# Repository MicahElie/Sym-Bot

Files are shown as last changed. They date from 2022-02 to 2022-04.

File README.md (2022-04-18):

# The Sym-Bot Project: A Robotic Arm by Hand Control 
## Sherbrooke University, Robotics Engineering S4 Project, 66th promotion, Winter 2022


<div align="center">
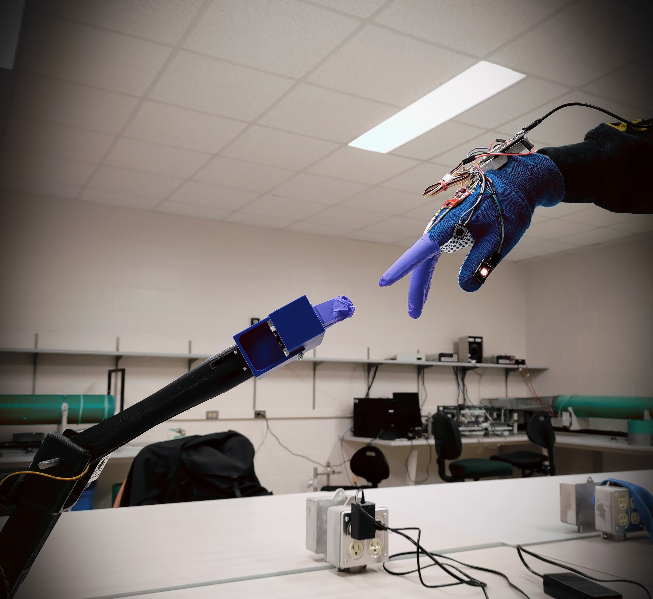
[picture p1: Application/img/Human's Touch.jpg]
Sym-Bot Human's Touch
    
</div>

## Table of Content
- [The Sym-Bot Project: A Robotic Arm by Hand Control](#the-sym-bot-project-a-robotic-arm-by-hand-control)
  - [Sherbrooke University, Robotics Engineering S4 Project, 66th promotion, Winter 2022](#sherbrooke-university-robotics-engineering-s4-project-66th-promotion-winter-2022)
  - [Table of Content](#table-of-content)
  - [Authors](#authors)
  - [Project context](#project-context)
  - [Abilities](#abilities)
  - [Important note](#important-note)
  - [Getting started](#getting-started)
    - [Mechanical recommandations](#mechanical-recommandations)
    - [Electrical recommandations](#electrical-recommandations)
    - [Software recommandations](#software-recommandations)
  - [Special Thanks](#special-thanks)

## Authors
- Andrei Ioan Gabor - [TerrySpooker](https://github.com/TerrySpooker)
- Julien Thériault - [JuThe72](https://github.com/JuThe72)
- Yan-Éric Jérôme - [Arasmith](https://github.com/Arasmith)
- Frank Ciric Taicas - [Chromlox](https://github.com/Chromlox)
- Frédérick Boisvert - [boif1403](https://github.com/boif1403)
- Micah-Élie Labrecque - [MicahElie](https://github.com/MicahElie)

## Project context
This project came up from the desire to help people with disabilities to take or move objects out of reach. 
More precisely, some of these people don't have enough strength in their arms to strech them out. Fortunately, most of the times, they can at least move their hands and fingers.
That's the core of the Sym-Bot Project : Using a glove with sensors to control a robotic arm in the most intuitive way possible, by working in **symbiosis** with the user.

## Abilities
Our robotic arm is a simple 3 degrees of freedom robot. The goal is to accomplish simple tasks only by using the "Glove controller". Here are four things that Sym-Bot can do:
1. Push/Pull an object on the table, placed in front of our robot
2. Turn switch On/Off, the switch being on the table
3. Take a cellphone (200g max.) and keep it in the air
4. Using AI to predict moves based on hand signs that we created

## Important note
Make sure to read all the documentation linked if you want to recreate your own Sym-Bot. 
We'll do anything we can so that the documentation is as clear as possible. First step, read the [Getting started](#getting-started) just below.

## Getting started
The first step to follow for building your own Sym-Bot application is to follow the READMEs step-by-step guide in each sections.
Our project is divided in three main sections: 
* The first one is [Application (Main Software)](Application/), that's **where all the communication and data interpretation between the Glove and the Robotic Arm is done**. In that section, you will mainly find the Python code that will go on the Raspberry Pi 4B (or any other computer of your choice) that will be linked to the OpenCR of the Robotic arm and the Bluetooth of the Glove. That's also where the [AI section](Application/AI/) is.
* The second section is [Robotic Arm](/Robotic%20Arm/), that's where **you'll find the C++ code for the motors control, all the 3D parts with the assembly models (SolidWorks) and the electrical schematic.**
* Finally, the last, but not least, part, is the [Glove User Interface](/Glove%20UI/), in this section **you'll find the C++ code used with PlatformIO on the ESP32 and the list of electrical sensors and components that are attached on the glove with the electrical schematic**.

### Mechanical recommandations
* Most of the parts of our robot arm should be 3D-printed.
* We used different kind of bolts, shafts, inserts and couplers
* We created our own bearing with metalic marbles, but you can easily modify this section
* The list of components to buy, 3D parts and the assembly of the robotic arm is in the [Material & Assembly section](/Robotic%20Arm/Material%20%26%20Assembly/)

### Electrical recommandations
* Most of the electrical part is on the implementation of sensors on the glove
* We personally sew the electrical components on the glove.
* Make sure to use long enough wires for the connection between the motors and the OpenCR
* For more information about the electrical design, look at the [Robotic Arm Electrical schematic](/Robotic%20Arm/Material%20%26%20Assembly/ElectricalSchematic_RoboticArm.png) and the [Glove Electrical schematic](/Glove%20UI/img/Electrical%20Schematic%20Glove.png)

### Software recommandations
* We mostly used Python and C/C++ with Visual Studio Code as code editor and IDE with extensions.

## Special Thanks
To [Handling GRO](https://github.com/chameau5050/Handling-Gro#handling-gro) for their robotic arm that inspired us to make our own.

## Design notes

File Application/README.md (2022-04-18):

# Sym-Bot : Application (Main Software)

## Table of Content
- [Sym-Bot : Application (Main Software)](#sym-bot--application-main-software)
  - [Table of Content](#table-of-content)
  - [Getting started](#getting-started)
  - [Communication](#communication)
    - [BluetoothComm](#bluetoothcomm)
    - [SerialComm](#serialcomm)
    - [Translate](#translate)
  - [AI](#ai)
  - [Interface](#interface)
  - [Test](#test)
    - [test translate class](#test-translate-class)

## Getting started
First, here's the hardware schematic that you have to keep in mind for every aspect of the project:
<div align="center">
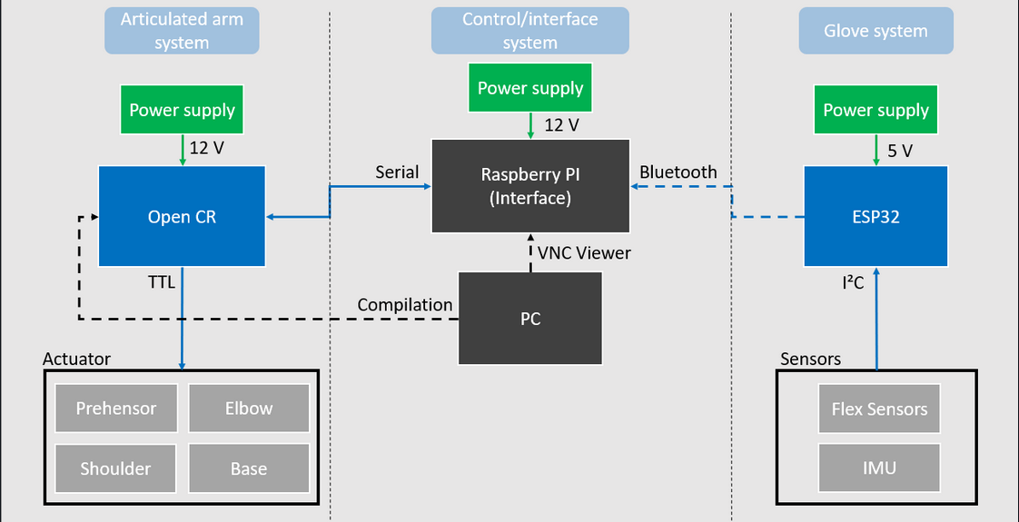
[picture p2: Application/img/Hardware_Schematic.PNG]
Hardware Schematic
    
</div>

***Setup environment***
- Software : [Visual Studio Code](https://code.visualstudio.com/) (Stable Build) and add extension Python, publisher Microsoft
- Using Python version (3.7 and newer)
- Installing packages from the Python with [command line](https://packaging.python.org/en/latest/tutorials/installing-packages/#installing-from-pypi) :
  - numpy (1.22.2)
  - pyserial (3.5)
  - pybluez (0.23)

Single board computer
* Brand : [RaspBerry Pi](https://www.raspberrypi.com/products/raspberry-pi-4-model-b/)
* Model : Raspberry PI 4 B
* Quantity : 1

## Communication
As you know, the Sym-Bot uses an ESP32, a Raspberry Pi 4 and an OpenCR Arduino microcontroller. All the code found in this section allows the communication between thoses devices to be functional. 
### BluetoothComm
Bluetooth Communication is used between Glove UI (ESP32) and Control System (PI4)

Steps to setup Bluetooth device (Must do before you launch main application) :
1. Turn on Bluetooth on Raspberry PI
2. Supply the device Bluetooth
3. Connect ESP32's device on Raspberry PI
4. Collect the informations device
* If you don't know the MAC & uuid device :
Using [rfcomm-client.py's example](https://github.com/pybluez/pybluez/blob/master/examples/simple/rfcomm-client.py) to find MAC & uuid device
5. Write "BT" to select bluetooth communication in main.py
```
10  # Select Communication's type between "USB" (Alternative proto-board UI) or "BT" (Glove)
11  TypeComm = "BT" 
```
6. Change the MAC & uuid device for yours
```
18      ''' Commmunication Bluetooth '''
19      MAC_ = '58:BF:25:37:A6:9A'                        # your MAC BT device
20      uuid_ = "00001101-0000-1000-8000-00805f9b34fb"    # your uuid BT device
```

### SerialComm
Serial communication is used between Control System (PI4) and Robotic Arm (OpenCr)

Steps to setup Serial device (Must do before you launch main application) :
1. Find the Serial Port of OpenCr Board (You can find this information with Arduino IDE -> Tools -> Ports)
2. Change port number on this line:
```
15  messageIO.addDevice(SerialComm("/dev/ttyACM0", 57600))  # Robotic Arm (OpenCr Board)
```
* On Windows OS, the Port Number starts with COM#
* On Linux OS, the Port Number starts with /dev/ttyACM# or /dev/USB#

### Translate
When the Bluetooth communication is established, it should receive messages in this form:
<div align="center">
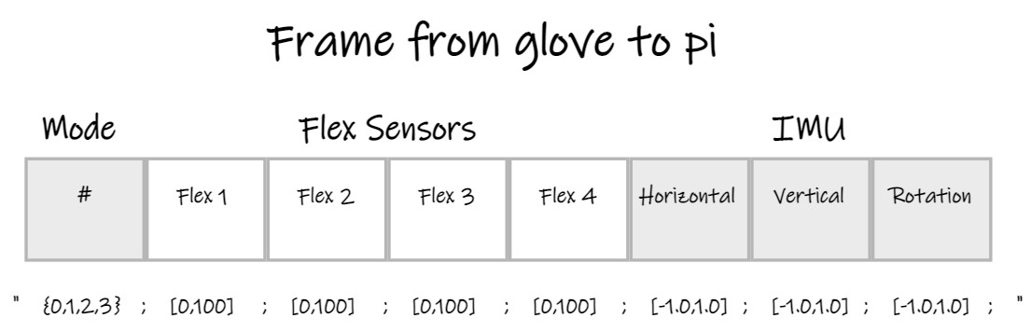
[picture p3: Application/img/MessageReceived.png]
Communication Protocol
    
</div>

As you can see, this message receives the mode, the flexion state of four fingers and information from the IMU. The strucutre used is a dictionary whith the keys "Mode", "Flex" and "IMU".
- Modes are linked with the "chooseMode()" function. It is possible to add others modes if you want, but make sure to use numbers that are used in this function
- Flexion states are linked with the "Flex" key of the dictionary and are used in every function of the translate class, depending on the way we want to translate the message
- Horizontal and vertical are not used in our application, but it could be used for knowing how your hand moves, vertically and horizontally. It's linked with the "IMU" key of the dictionary
- Rotation is also linked with the "IMU" key and it is used to know if your hand is upside-down or not. It's also used in every function of the translate class. In our particular case, the orientation of the hand indicates in which direction you want to control the motor.

As it was stated before, it is possible to add an other mode. It also means that you may want to add another function in the translate class. Here's how you should do it:
- Add mode in chooseMode() and execute the name of your new function in the if clause.
```
if msgGlove['Mode'] == modeNumber:
  self.mode = msgGlove['Mode']
  self.jogMode(msgGlove["oneOfTheKeys"], msgGlove["oneOfTheKeys"])
```
- Make sure to create the function linked with a new translation
```
def yourNewMode(self, "oneOfTheKeysYouSent", "oneOfTheKeysYouSent"):
  ##your new translation
```
- Make sure to send messages in the right format, using ControlMessage and MessageIO class(create a MessageIO object). These classes make your messages readable for the OpenCR. You also have to add a constant linked to your mode in ControlMessage.py
```
msg_to_motor = ControlMessage(ControlMessage.yourOwnConstant, self.youMessage)
self.msgIO.sendMessage(0, msg_to_motor)
```
Note that in our application, the message sent to the motors are in the form: `[motor1,motor2,motor3,servoMotor]`. In other words, its a message for each motor used.

## AI
[AI section click here](/Application/AI/)

## Interface
The interface is built thanks to guizero, an easy to install (and to use) module.
To integrate the Interface into the code, we must include the file. Don't forget to display() at the end. The update_command function must be used in the main to change the functions attached to the buttons. We must link the labels of X, Y, Z, J1, J2 and J3 so that it shows real time values. We must also make variables that will be linked to the state of the gripper and wether we are in Cartesian or Joint mode. We should add an update function so that the info can stay up-to-date.

## Test
### test translate class
This test class looks mainly at the chooseMode or jogMode method. It verifies if the right mode is passed to the other class, if the IMU is taken into account and if the rigth message is sent according to what was received. If you run this test, you should see "OK". At the end of this project, a modification made by another member created an error that we didn't have time to correct. The error code shown when you run the test should help you debug this test.

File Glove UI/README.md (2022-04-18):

# Sym-Bot : User Interface Glove

<div align="center">
    Glove Assembly
</div>

## Table of Content
- [Sym-Bot : User Interface Glove](#sym-bot--user-interface-glove)
  - [Table of Content](#table-of-content)
  - [Material](#material)
    - [Electrical Components](#electrical-components)
    - [Other components](#other-components)
  - [Electrical Schematic](#electrical-schematic)
  - [Getting started](#getting-started)
    - [Environnement setup](#environnement-setup)
    - [Running the code](#running-the-code)
    - [Recommendations](#recommendations)
  - [How to use the Sym-Bot Glove with the Robotic Arm](#how-to-use-the-sym-bot-glove-with-the-robotic-arm)
  - [Alternative](#alternative)

## Material
### Electrical Components
- #### ESP32 microcontroller
  * Brand : [Espressif inc.](https://www.espressif.com/en/products/devkits/esp32-devkitc/overview)
  * Model : DOIT ESP32 DEVKIT v1
  * Quantity : 1 

- #### Flex Sensor
    * Brand : [SparkFun](https://www.sparkfun.com/products/14666)
    * Mdoel : SparkFun Qwiic Flex Glove Controller
    * Quantity : 2
    * **Note: You can also use individual flex sensors, that will change the code implementation, because the data communication will not be I2C.** 

- #### IMU
  * Brand : [Grove-SeeedStudio](https://wiki.seeedstudio.com/Grove-IMU_9DOF_v2.0/)
  * Model : IMU 9DOF v2.0
  * Quantity : 1

- #### Power Supply
  * Brand : [EnergyCell Mini](https://www.amazon.ca/-/fr/EnergyCell-chargeur-portable-5000-compatible/dp/B09JNSVJD4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)
  * Model : Black
  * Quantity : 1
  * **Note: You can use your own power bank of 5V with at least 1250mAh, depends on your glove's time usage with one charge.**
  
- #### RGB LED module
  * For example: [LED RGB module](https://fr.banggood.com/3-Colour-RGB-SMD-LED-Display-Module-5050-Full-Color-p-90626.html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)
- #### Button
- #### Some Wires
- #### Breadboard (for testing)

### Other components
- #### Gardening Gloves
- #### Medical Gloves (each finger of the gardening glove should fit inside the medical glove)

## Electrical Schematic
<div align="center">
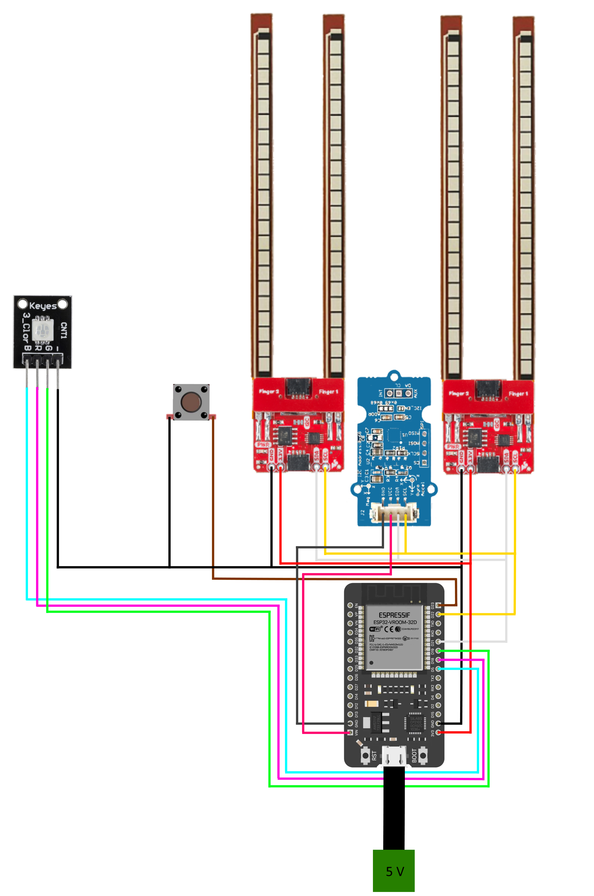
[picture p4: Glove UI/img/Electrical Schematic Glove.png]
Glove Electrical Schematic
    
</div>

*Refer also to the [picture](#sym-bot--user-interface-glove) above for assembly*

## Getting started
### Environnement setup
First, you'll neeed to install [Visual Studio Code](https://code.visualstudio.com/Download)

When you open Visual Studio Code, go to the Extensions section PIO Extensions Button search for the extension [PlatformIO](https://marketplace.visualstudio.com/items?itemName=platformio.platformio-ide) and finally, install it.

### Running the code
Once everything is installed, you can click on the little Home button PIO Home Button that is on the bottom blue bar, near the left side. 

Then go to Open Project
<div align="center">
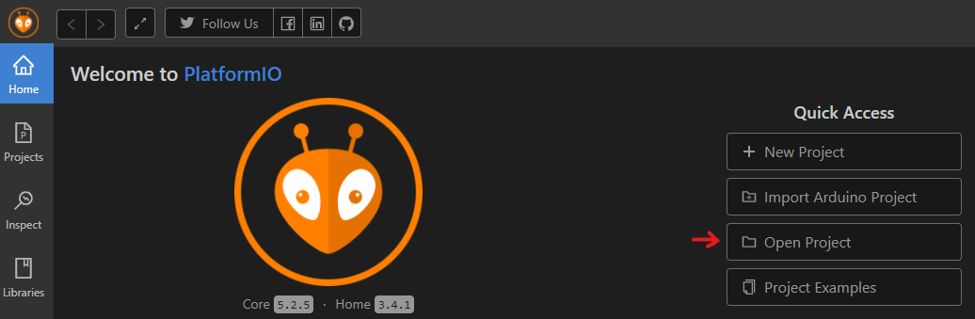
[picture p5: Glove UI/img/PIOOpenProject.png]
Open Project image guide
  
</div>
Search and choose to open the Glove folder

That's it! Now you are ready to Build and Compile PIO Build and Compile the code on the DOIT-ESP32 Devkit v1

### Recommendations 

If you're running into some troubles with the DOIT-ESP32 Devkit v1 [check this site](https://randomnerdtutorials.com/esp32-troubleshooting-guide/). **I personally had to follow the 6th troubleshooting(COM port not found) for using for the first time the DOIT-ESP32 Devkit v1.**

More information on setting up [DOIT-ESP32 Devkit v1](https://docs.platformio.org/en/latest/boards/espressif32/esp32doit-devkit-v1.html) with PlatformIO.

You can also change the type of board and some other settings in the file [platformio.ini](https://docs.platformio.org/en/latest/projectconf/index.html). 

## How to use the Sym-Bot Glove with the Robotic Arm

To control the robotic arm with the glove, there are three modes available:

- The first one is Jog Mode with the orange LED, in this mode you control individually each motor of the robotic arm by closing either the index, middle or/and ring finger(s) and the orientation of the rotation of the motor with the orientation of the hand. The pinky closes or opens the gripper.
- The second mode is Cartesian Mode with the green LED, in this mode you can control with precision the gripper and normally you can move horizontally the gripper with the index and vertically with the middle finger. With the ring finger you can control the base rotation. This mode doesn't work well right now, it is in early development.
- Finally, we have the Gesture Mode (AI) with the blue LED, in this mode you control the robotic arm with gestures. We only added three gestures for now:
  - The first one is with only the index open and the others fingers closed and the palm of the hand facing the ground (like pointing something)
  - The second one is the same as the first one, but the palm is facing up.
  - The last is just all the fingers closed.
  
  So, the first gesture makes the robot do a pick animation, the second is a drop animation and the last is go to Home position. This mode is also in early development.

## Alternative
The symbotUIproto code provided can be used with the Arduino Mega 2560 ATmega. This code uses USB Serial communication with the main.py in Application folder. You can use it with the JOG and JOINT mode that are in translate.py to control the robotic arm. 

To help you recreate the proto-board shield that goes on the Arduino Mega, here's an electrical schematic with a picture.
<div align="center">
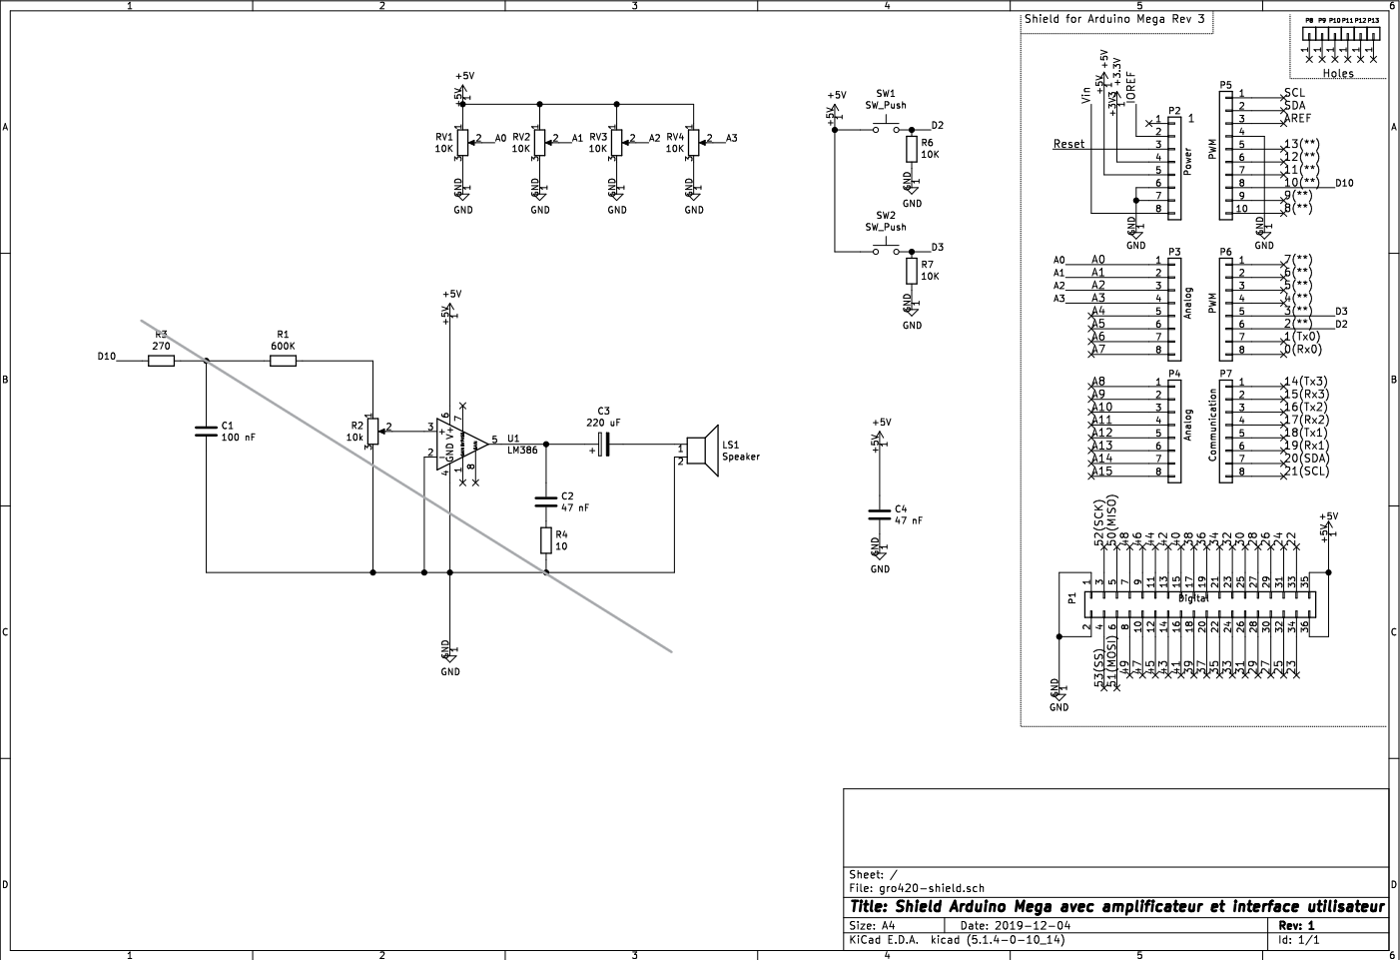
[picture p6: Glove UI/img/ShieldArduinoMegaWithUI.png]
Electrical Schematic - Shield Arduino Mega With UI
  
  <p>Electrical schematic of the proto-board</p>
</div>

<div align="center">
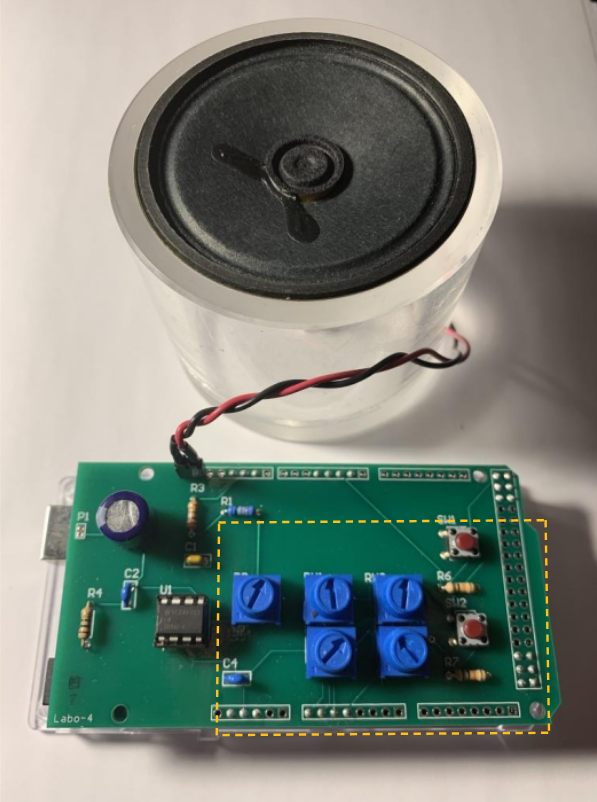
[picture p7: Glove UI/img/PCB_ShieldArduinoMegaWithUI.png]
PCB Shield Arduino Mega With UI
    
    <p>PCB shield used to mock the glove</p>
</div>

***Images from the Proto-Board are provided by University of Sherbrooke from the Robotics Engineering program and with the autorisation of François Ferland***

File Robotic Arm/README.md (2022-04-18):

# Sym-Bot : Robotic Arm

<div align="center">
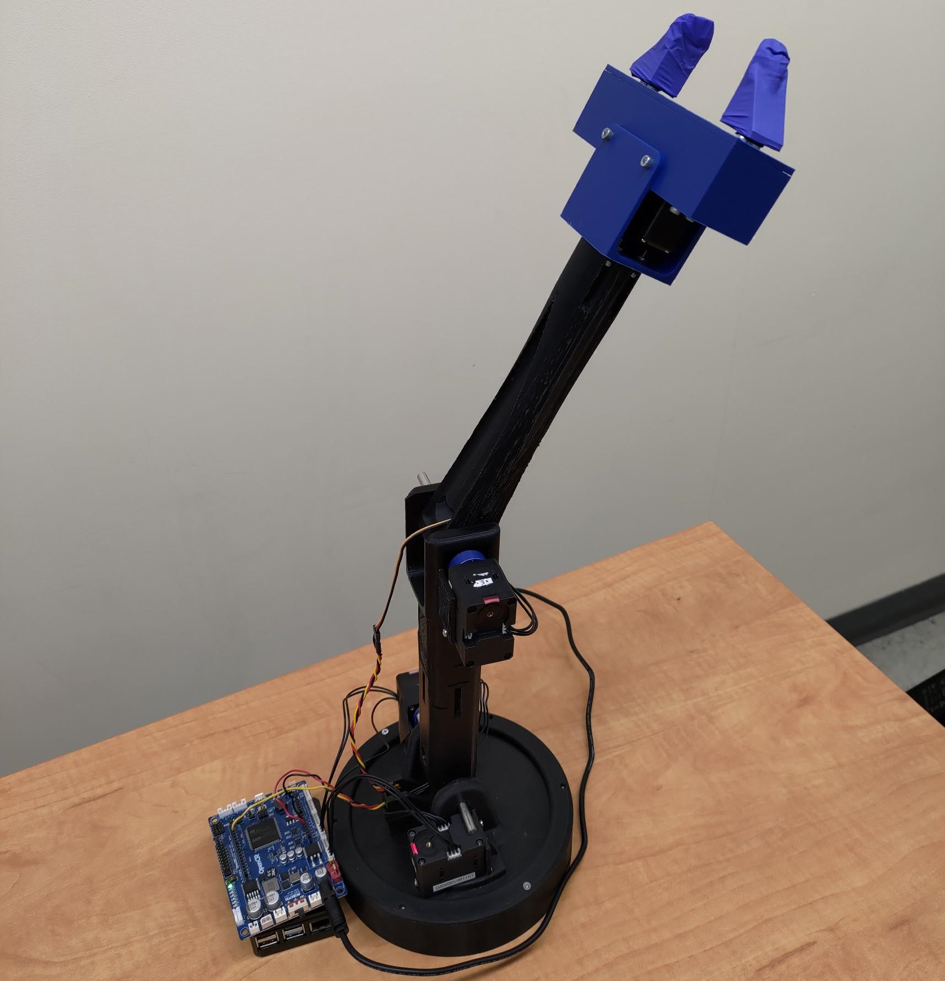
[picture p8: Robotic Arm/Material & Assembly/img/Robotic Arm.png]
Sym-Bot Human's Touch
    
</div>

## Table of Content
- [Sym-Bot : Robotic Arm](#sym-bot--robotic-arm)
  - [Table of Content](#table-of-content)
  - [Material & Assembly](#material--assembly)
  - [Motor Control](#motor-control)

## Material & Assembly
In this [folder](/Robotic%20Arm/Material%20&%20Assembly), you will find:
1. List of pieces needed to assemble the robotic arm
2. Drawings (SW) and models (STL)
3. Assembly guide
4. Electrical schematics for the OpenCR card and its attached motors

## Motor Control
In this [folder](/Robotic%20Arm/MotorControl), you will find:
1. C++ code to manually calibrate the motors (Due to the lack of positional sensors)
2. C++ code responsible for motor control and serial communication

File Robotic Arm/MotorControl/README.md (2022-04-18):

# Sym-Bot : Motor Control

## Table of Content
- [Sym-Bot : Motor Control](#sym-bot--motor-control)
  - [Table of Content](#table-of-content)
  - [Environment](#environment)
  - [Calibration](#calibration)
  - [Control](#control)

## Environment
- Software : [Arduino IDE](https://www.arduino.cc/en/software) (1.8.19)
- Add OpenCr board (1.6.4) with instructions : https://emanual.robotis.com/docs/en/parts/controller/opencr10/#arduino-ide
- Add library ArduinoJson (6.18.5) with Libray Manager
- Optional : Using [Visual Studio Code](https://code.visualstudio.com/) like a source-sode editor and add extension Arduino, publisher Microsoft
- WARNING : The codes below uses the versions mentioned in above (#.#.#).

## Calibration
With monitor_m, we can get the different motor's position
1. Open Serial Monitor after uploading the code
2. Write "begin [baudrate]" to initialise the communication with motor(s)
3. Write "scan [range]" to find the motor's id
4. Write "joint (id)" to set joint mode | Foreach motor
5. Write "torque (id) 0" to disable torque | Foreach motor
6. Position the robot at its zero
7. Write "position (id)" to get present position from motor | Foreach motor
8. Transcribe the results into main code, function init_dynamix()
9. Repeat step [6,8] for different position
10. If motor doesn't rotate in good direction, you can write "counter_clockwise (id)" or "clockwise (id)"

* Write what is in the quotation marks to Serial Monitor, [] => optional number and () => must number

## Control
With main, we can upload the code to control the robotic arm.

Before uploading the OpenCR Microcontroller code , make sur that the values defined in the init_dynamix() and init_servo() functions coresponds to your articulated arm implementation

After uploading the code on the OpenCr Board, you can test the communication by writing directly to the monitor serial (Arduino IDE)<br>
Summary for JSON message :
- "type": Define the command, [1,9] : Action cmd, [11,19] : Set command & [21,29] : Return command
- "PLS" : Length of data
- "data": Data for motors [J1,J2,J3,Gripper] (Ignore when it's return command, store the informations)
Example :
- {"type":1,"PLS":4,"data":[180,45,90,180]} => HOME Position in JOINT MODE
- {"type":2,"PLS":4,"data":[180,45,90,180]} => Set Robotic Arm in HOME Position
- {"type":3,"PLS":4,"data":[0,1,-1,1]}      => [Not move, Foward, Backward, Close] in JOG MODE, Only once
- Repeat {"type":3,"PLS":4,"data":[0,1,-1,1]} to keep jog
- {"type":27,"PLS":4,"data":[0,0,0,0]}      => Return the actual position the each motor in data (step unit)

<div>
  <h4>Class Diagram Main</h4>
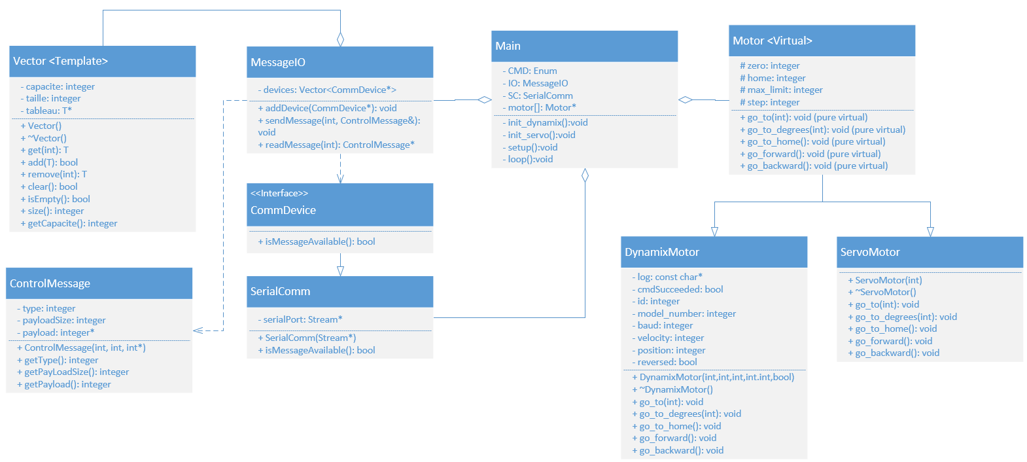
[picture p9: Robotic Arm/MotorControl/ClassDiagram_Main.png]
Class Diagram Main
  
</div>

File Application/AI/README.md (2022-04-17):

# Sym-Bot : AI

## Table of Content
- [Sym-Bot : AI](#sym-bot--ai)
  - [Table of Content](#table-of-content)
  - [Setup](#setup)
  - [Training](#training)
  - [Adding Actions](#adding-actions)

## Setup
- Software : PyCharm (2021.3.1)
- Language : Python (3.9)
- Packages : 
  - numpy (1.22.2)

## Training
Training examples for the AI are stored within the "Symbot_Data_Set.txt" CSV file. The name of the file can be specified in the <i>translate</i> class (<i>Comm/translate.py</i>) under the variable <i>file_data_set</i>.

Before training the AI, make sure the following conditions are met:
- <i>DEVELOPPER_MODE</i> (<i>translate.py</i>) is set to True
- <i>print(msg)</i> lines in <i>main.py</i> are commented out
- <i>N_ACTIONS</i> in <i>translate.init</i> corresponds to the correct amount of possible actions (see [Adding Actions](#adding-actions))
- Connection with glove is ready to be established
- Access to PyCharm terminal (VSCode also works, but the team had issues with it and recommends using PyCharm)

Then, execute the program as normal (from <i>main.py</i>). To add a new training example, follow these steps:
1. Equip the glove
2. Execute the desired hand sign
3. Label the action by entering its corresponding number in the terminal

Here are some tips to improve the efficiency of the AI:
- "Reset" the position of your fingers between every example
- Add some variety to your hand signs (Flex your fingers a bit more or less, rotate your wrist, etc.)
- Make sure the flex sensors readings are reasonable (You can always manually delete a line from the CSV file if necessary)

## Adding Actions
The current implementation of the AI only allows simple instructions in the form of a sequence of hard-coded positions. To add or change an action, simply modify the <i>manageAction</i> function in the <i>translate</i> class accordingly. The sequence is described as follow:
- Sequence : [POSITION_1, POSITION_2, ..., POSITION_N]
- Position : [JOINT_1, JOINT_2, JOINT_3, GRIPPER]

With the following ranges:
- JOINT_1 : [0, 360]
- JOINT_2 : [0, 90]
- JOINT_3 : [0, 90]
- GRIPPER : [0, 180]

Note that to prevent issues with the motors, avoid going to the limits of their corresponding ranges.

To make sure the command is treated accordingly, the value of <i>N_ACTIONS</i> in <i>translate.init</i> should correspond to the maximum value of the <i>elif</i> clause. It's also possible to implement a default <i>else</i> clause to englobe all non-implemented actions.

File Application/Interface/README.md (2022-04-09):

This interface was made using guizero. You can find information on how to download and use guizero here: https://lawsie.github.io/guizero/ Further information about how to add and configure widgets can be found under the widget tab of that website.

The point of this interface is to test out functions on the arm without the glove and vice-versa. This is done using buttons, which send commands to the arm. The move button next to the coordinates allows the user to input a coordinate of his choice. Once the coordinates have been registered, the user may send them using the send button. The open and close gripper buttons glow according to the state of the gripper. The cartesian/joint mode buttons allow to switch states (theoretically).

The images in this folder are important. They are the images for the gripper buttons. If you delete them, the code will no longer be able to access them and the buttons will be blank.

Ideally, there would be a retroaction between the state of the arm and the interface. Ideally, there would also be a way to show the state of the glove on the interface.

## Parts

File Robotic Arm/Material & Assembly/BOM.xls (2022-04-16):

ITEM NO. | PART NUMBER | DESCRIPTION | QTY.
1 | Base | 3D printed | 1
2 | Holding_Ring | 3D printed | 1
3 | Arm_base | 3D printed | 1
4 | Rotation_Gear | 3D printed | 1
5 | Gear_Shaft | 3D printed | 1
6 | Coupler Medium | 3D printed | 1
7 | Coupler350W | 3D printed | 2
8 | M3 brass insert |  | 6
9 | M6 brass insert |  | 4
10 | 545548_hub | Kit Actobotics | 6
11 | 5-16_Stainless_Steel_Ball |  | 49
12 | XL430-W250 | Dynamixel motor | 1
13 | XM430-W350 | Dynamixel motor | 2
14 | Arm_1A | 3D printed | 1
15 | Arm_1B | 3D printed | 1
16 | Arm_2 | 3D printed | 1
17 | shaft | 1/8" 3" long D shaft | 2
18 | base_1 | 3D printed | 1
19 | base_2 | 3D printed | 1
20 | claw_rack | 3D printed | 2
21 | claw_tip | 3D printed | 2
22 | driving_gear | 3D printed | 1
23 | adaptor | 3D printed | 1
24 | #6 Nylon washer | Kit Actobotics | 8
25 | 1/4" Spacer | Kit Actobotics | 4
26 | hs-422 | Hitec 180 degree servomotor | 1
27 | horn cross | Hitec cross-shaped adaptor | 1
28 | M3 10mm screw | M3 10mm cone head screw | 6
29 | M3 10mm screw | M3 10mm socket head screw | 4
30 | M3 20mm screw | M3 20mm socket head screw | 4
31 | M3 hex nut | M3 screw hexagonal nut | 8
32 | 6-32 3/4" screw | 3/4” x 6-32 Zinc-Plated Socket Head Screw | 14
33 | 6-32 1/2" screw | 1/2” x 6-32 Zinc-Plated Socket Head Screw | 1
34 | 6-32 3/8" screw | 3/8” x 6-32 Zinc-Plated Socket Head Screw | 8
35 | 6-32 1/4" screw | 1/4” x 6-32 Zinc-Plated Socket Head Screw | 1
36 | 6-32 hex nut | 6-32 screw hexagonal nut | 14
37 | 585474 screw plate | 6-32 screw square nut | 2

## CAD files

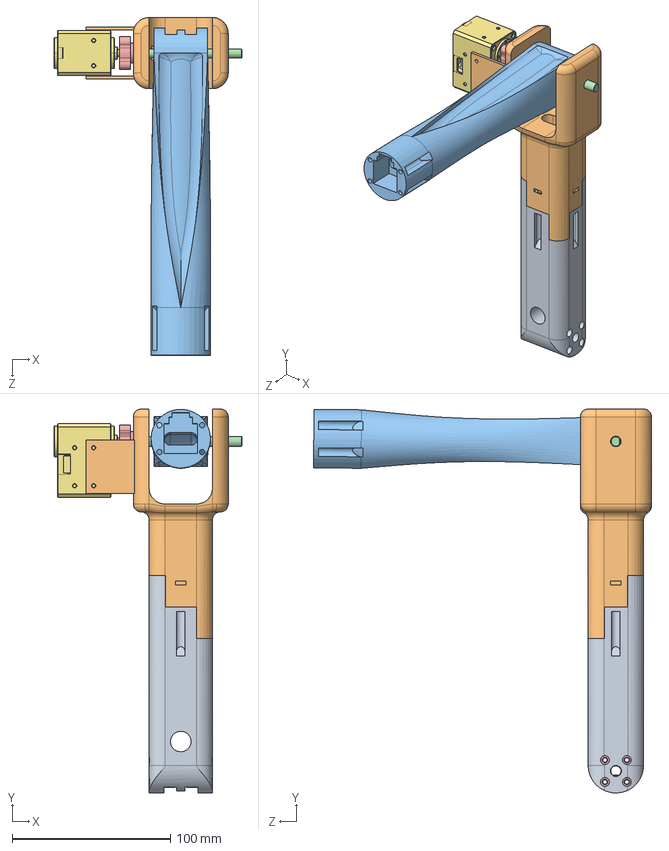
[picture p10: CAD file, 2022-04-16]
Robotic Arm/Material & Assembly/Arm/Arm.SLDASM
118.6 x 242.5 x 213.5 mm
Arm_1A
Arm_1B
Arm_2
shaft
545548.STEP x 5
632138_91375A438.STEP x 5
XM430-W350

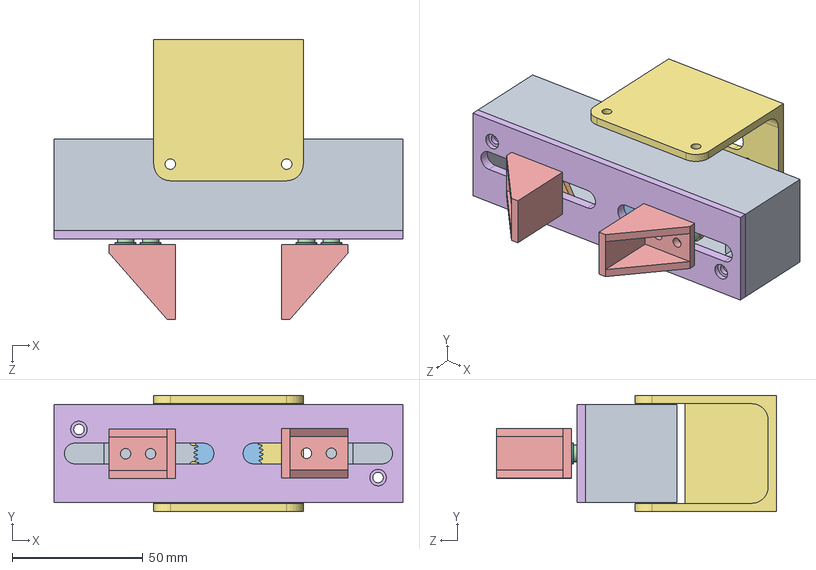
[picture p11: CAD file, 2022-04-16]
Robotic Arm/Material & Assembly/Gripper/gripper_assy.SLDASM
133.4 x 44.5 x 107.0 mm
base_1
claw_rack x 2
driving_gear
spacer x 4
claw_tip x 2
base_2
adaptor
washer x 8

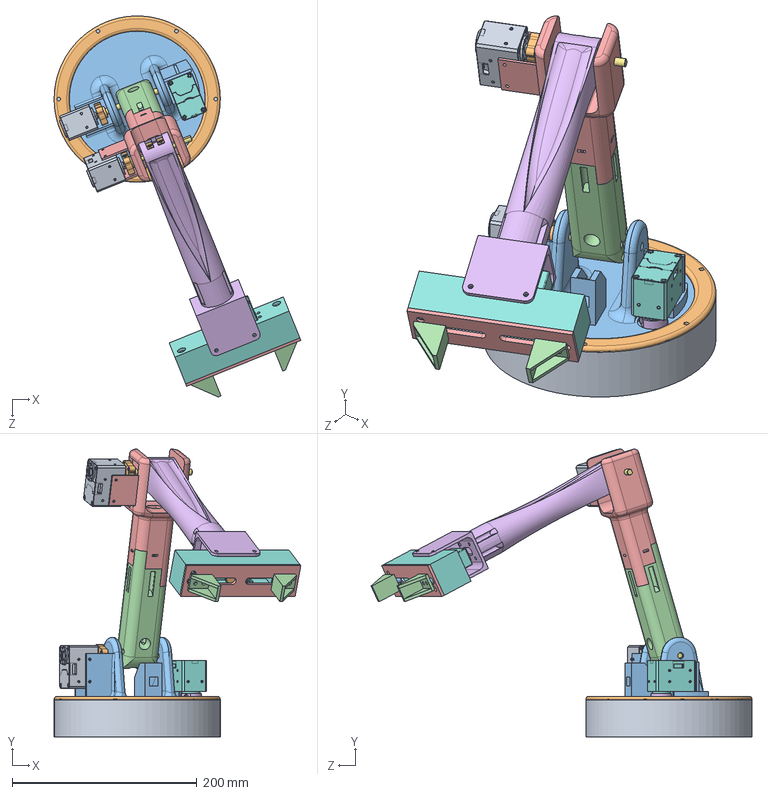
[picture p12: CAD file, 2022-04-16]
Robotic Arm/Material & Assembly/Sym-Bot.SLDASM
267.3 x 311.9 x 412.8 mm
Base
Holding_Ring
Arm_Base
Rotation_Gear
5-16_Stainless_Steel_Ball x 45
Coupler_Medium
Gear_Shaft
XL430-W250
XM430-W350 x 2
545548.STEP x 6
632138_91375A438.STEP x 6
Arm_1A
Arm_1B
Arm_2
shaft x 2
base_1
claw_rack x 2
driving_gear
spacer x 4
claw_tip x 2
base_2
adaptor
washer x 8
servo body.stp
servo output.stp

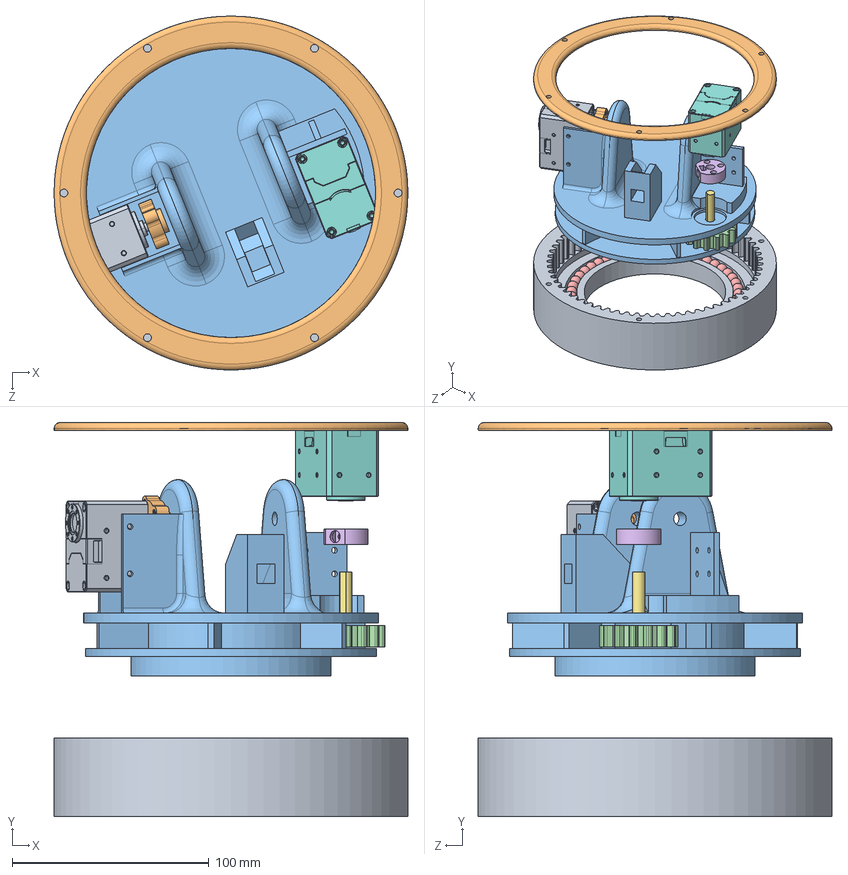
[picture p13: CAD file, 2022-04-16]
Robotic Arm/Material & Assembly/Base/Base.SLDASM
180.0 x 200.4 x 180.0 mm
Base
Holding_Ring
Arm_Base
Rotation_Gear
5-16_Stainless_Steel_Ball x 49
Coupler_Medium
Gear_Shaft
XL430-W250
XM430-W350
545548.STEP
632138_91375A438.STEP

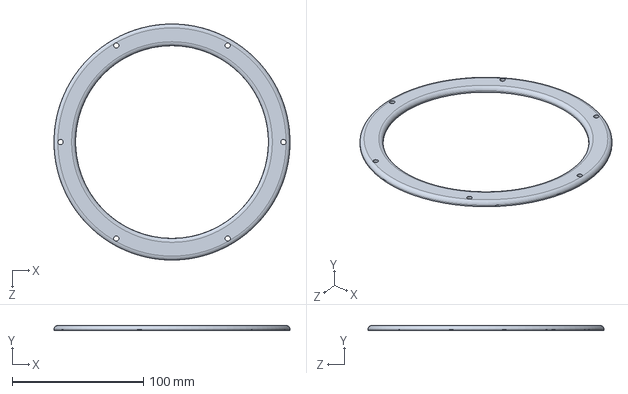
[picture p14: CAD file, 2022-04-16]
Robotic Arm/Material & Assembly/Base/Holding_Ring.SLDPRT
180.0 x 4.00 x 180.0 mm

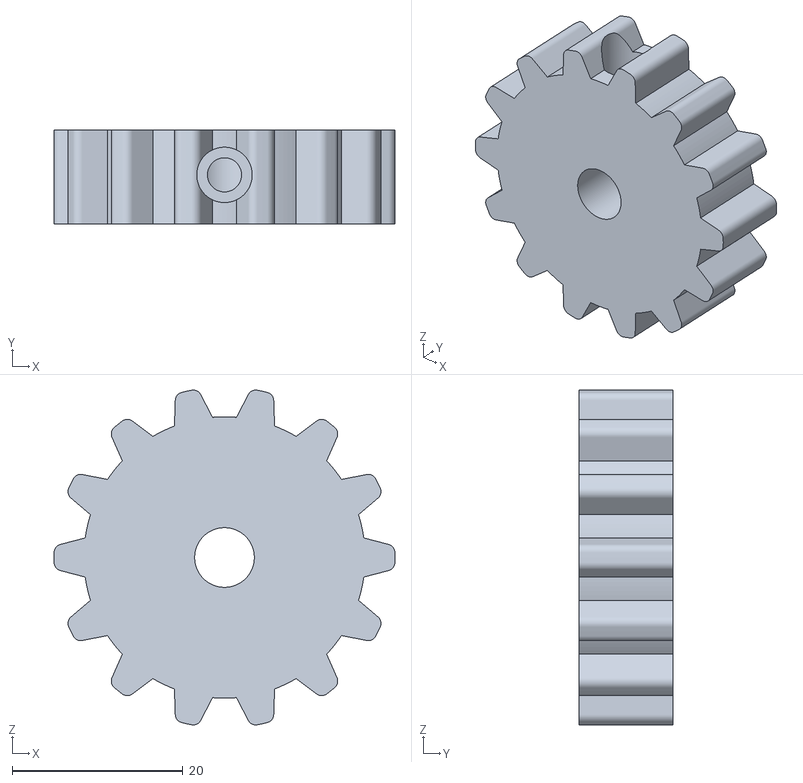
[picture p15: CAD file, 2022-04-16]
Robotic Arm/Material & Assembly/Base/STL/Driving_Gear.STL
40.0 x 11.0 x 39.3

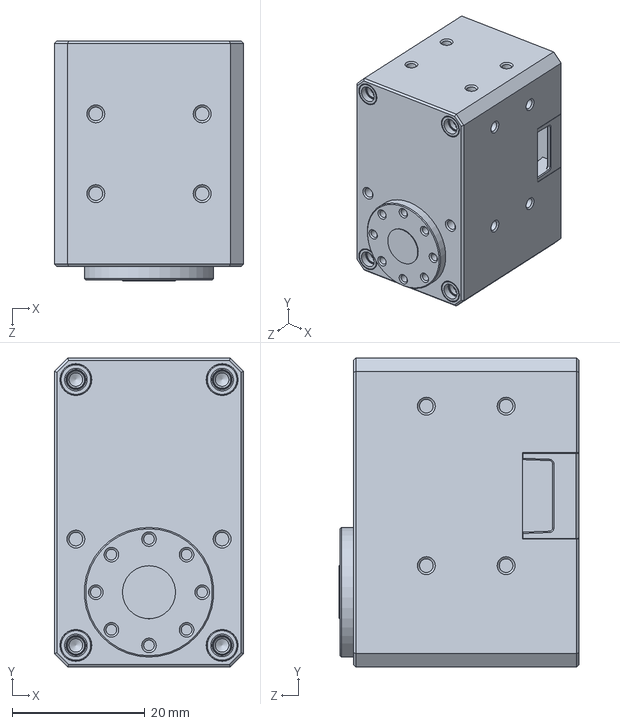
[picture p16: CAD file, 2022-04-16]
Robotic Arm/Material & Assembly/Electronics/XL430-W250.SLDPRT
28.5 x 46.5 x 36.2 mm

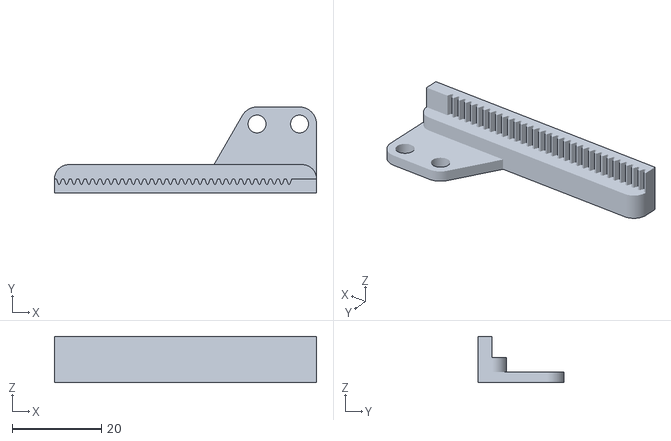
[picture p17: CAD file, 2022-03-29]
Robotic Arm/Material & Assembly/Gripper/STL/claw_rack_V2.STL
58.7 x 19.3 x 10.3

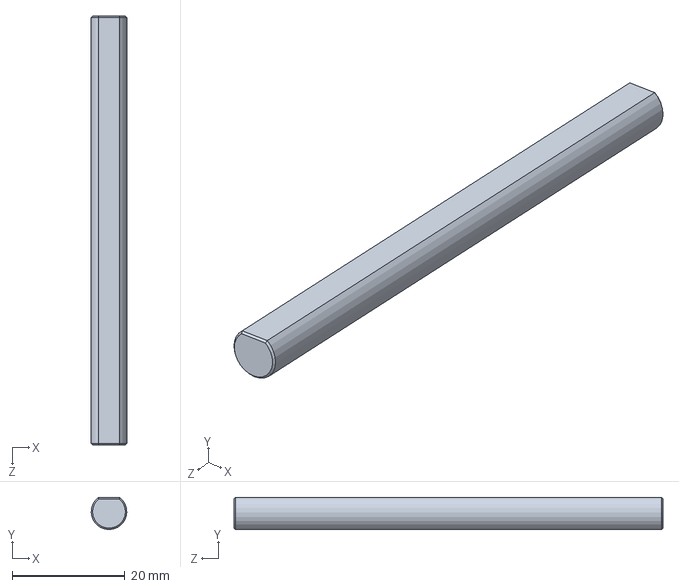
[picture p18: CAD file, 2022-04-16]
Robotic Arm/Material & Assembly/Miscellaneous/shaft.SLDPRT
6.34 x 5.72 x 76.2 mm

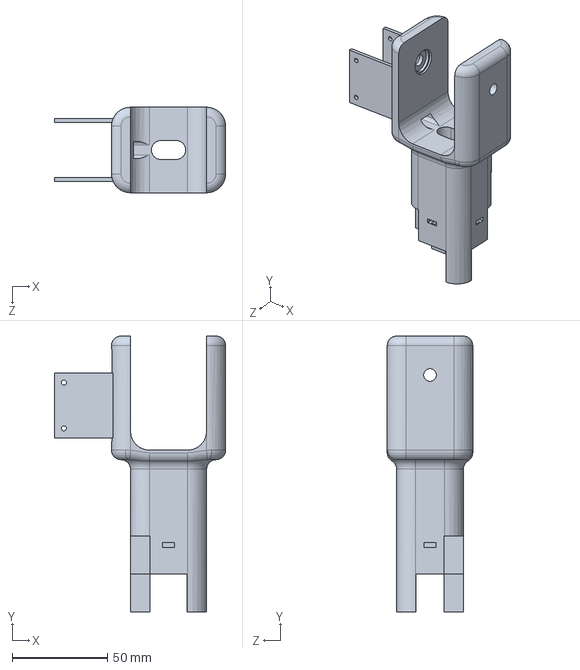
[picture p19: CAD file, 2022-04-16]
Robotic Arm/Material & Assembly/Arm/Arm_1B.SLDPRT
90.0 x 145.0 x 45.0 mm

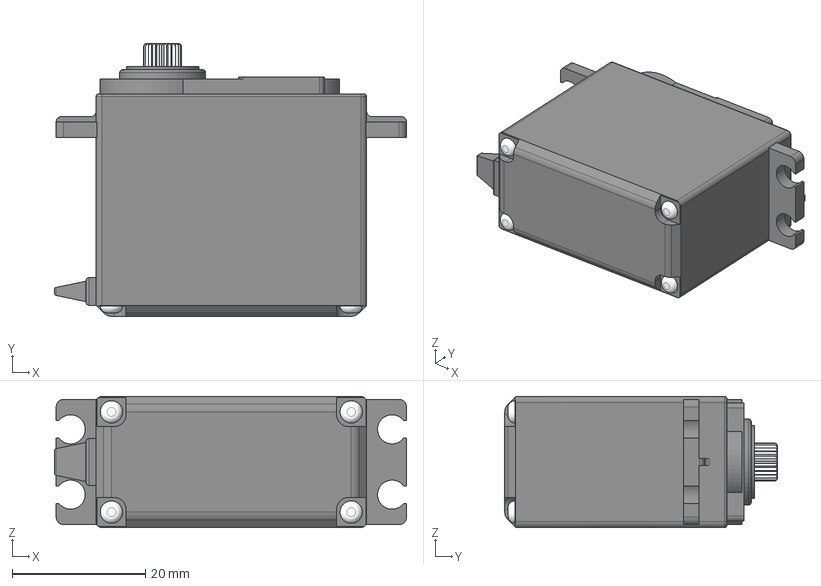
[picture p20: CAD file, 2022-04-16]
Robotic Arm/Material & Assembly/Electronics/hs-422.stp
52.8 x 40.9 x 19.7 mm

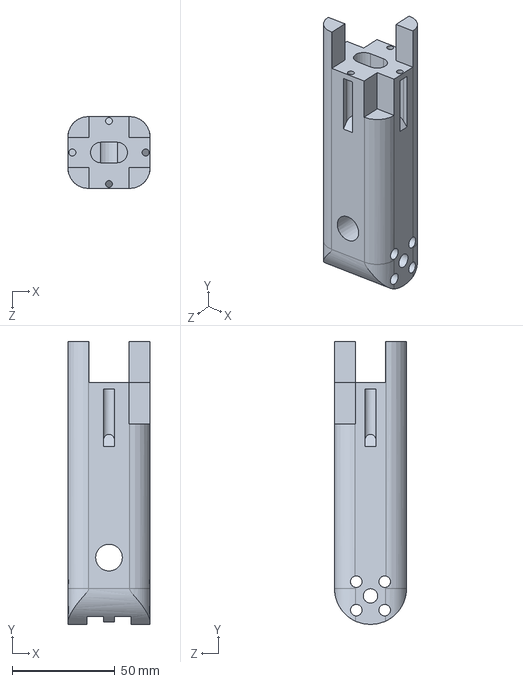
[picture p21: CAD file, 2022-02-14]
Robotic Arm/Material & Assembly/Arm/Arm_1A.SLDPRT
40.0 x 137.5 x 35.0 mm

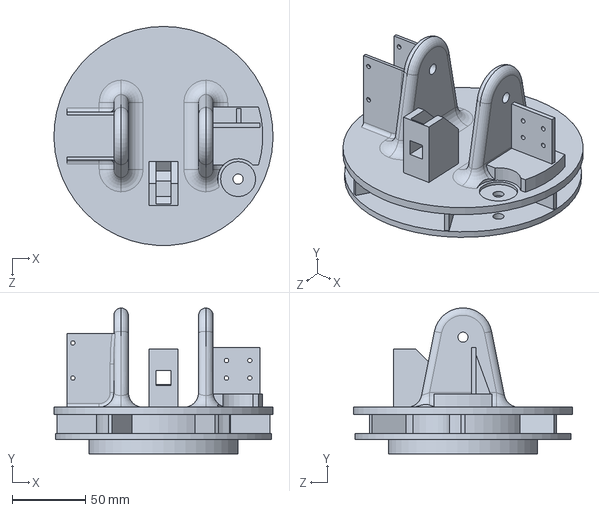
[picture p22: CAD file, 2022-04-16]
Robotic Arm/Material & Assembly/Base/Arm_Base.SLDPRT
149.9 x 99.9 x 150.0 mm

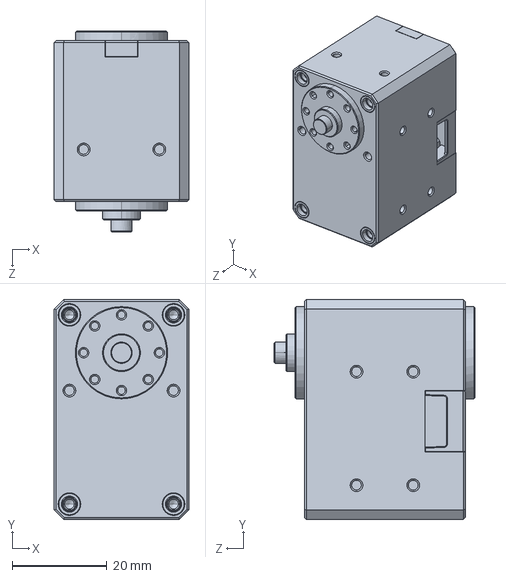
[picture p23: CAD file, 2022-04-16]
Robotic Arm/Material & Assembly/Electronics/XM430-W350.SLDPRT
28.5 x 46.5 x 42.4 mm

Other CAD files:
Robotic Arm/Material & Assembly/Base/Rotation_Gear.SLDPRT
Robotic Arm/Material & Assembly/Gripper/base_1.SLDPRT
Robotic Arm/Material & Assembly/Miscellaneous/coupler350W.SLDPRT
Robotic Arm/Material & Assembly/Arm/Arm_2.SLDPRT
Robotic Arm/Material & Assembly/Arm/Arm.SLDDRW
Robotic Arm/Material & Assembly/Arm/STL/Arm_1A.STL
Robotic Arm/Material & Assembly/Arm/STL/Arm_1B.STL
Robotic Arm/Material & Assembly/Arm/STL/Arm_2.STL
Robotic Arm/Material & Assembly/Base/5-16_Stainless_Steel_Ball.SLDPRT
Robotic Arm/Material & Assembly/Base/Base.SLDPRT
Robotic Arm/Material & Assembly/Base/Coupler_Medium.SLDPRT
Robotic Arm/Material & Assembly/Base/Gear_Shaft.SLDPRT
Robotic Arm/Material & Assembly/Base/STL/Arm_Base.STL
Robotic Arm/Material & Assembly/Base/STL/Base.STL
Robotic Arm/Material & Assembly/Base/STL/Coupler_Medium.STL
Robotic Arm/Material & Assembly/Base/STL/Gear_Shaft.STL
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

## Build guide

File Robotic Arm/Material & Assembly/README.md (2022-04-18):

# Material and Assembly

## Table of Content
- [Material and Assembly](#material-and-assembly)
  - [Table of Content](#table-of-content)
  - [Electrical Components](#electrical-components)
    - [MicroController](#microcontroller)
    - [Dynamixel Motors 1](#dynamixel-motors-1)
    - [Dynamixel Motors 2](#dynamixel-motors-2)
    - [ServoMotors](#servomotors)
    - [Power Supply](#power-supply)
  - [Assembly Info](#assembly-info)
    - [couplerW350](#couplerw350)
    - [Gripper](#gripper)
  - [Electrical Schematic](#electrical-schematic)

## Electrical Components
### MicroController
* Brand : [OpenCr](https://www.robot-advance.com/art-opencr1-0-robotis-2353.htm)
* Model : OpenCr
* Quantity : 1

### Dynamixel Motors 1
* Brand : [Dynamixel](https://emanual.robotis.com/docs/en/software/dynamixel/dynamixel_workbench/)
* Model : XM430-W350
* Quantity : 1

### Dynamixel Motors 2
* Brand : [Dynamixel](https://emanual.robotis.com/docs/en/software/dynamixel/dynamixel_workbench/)
* Model : XM430-W250
* Quantity : 2

### ServoMotors
* Brand : [HiTec](https://www.robotshop.com/ca/en/hitec-hs-422-servo-motor.html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)
* Model : HS-422
* Quantity : 1

### Power Supply
* Brand : [GlobTek inc.](https://www.digikey.ca/en/products/detail/globtek-inc/TR9CE7500LLP-IM-R6B/11201299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)
* Model : GTM96900P9012-T2
* Quantity : 1

## Assembly Info
Assembly schematics and BOMs for each part of the robot (gripper, arm and base) are available in "Material and Assembly" -> "Assembly". Parts that need to be printed can be found in their respective "STL" folder.

### couplerW350
The XM430-W350 Dynamixel motors use a particular coupler in order to support higher torques. The couplerW350 (available under "Miscellaneous") functions as a bridge between the motor and the 545548 hub. To properly assemble the coupler, the following screws should be used:
* 4 x M2x03 socket head
* 4 x 6-32x1/4 socket head

### Gripper
Due to its compactness, the gripper should be assembled in a specific order to tighten every screws properly.
* Assemble the claw tips and the racks through the slots of the casing using the appropriate spacers and washers in between.
* Fix the HS-422 Hitec servomotor to the casing. In order to protect the casing, the use of washers is recommended, but not necessary.
* Install the adaptor. Make sure the cables of the Hitec servomotor bend in a natural way to avoid permanent damage.
* Screw the two parts of the casing together. Make sure the driving gear is in its "open" state by turning it clockwise until it blocks before connecting it with the racks.
* Gently push the claw tips toward each other. If everything went well, the gear should rotate along. The gripper is now ready to use.

## Electrical Schematic
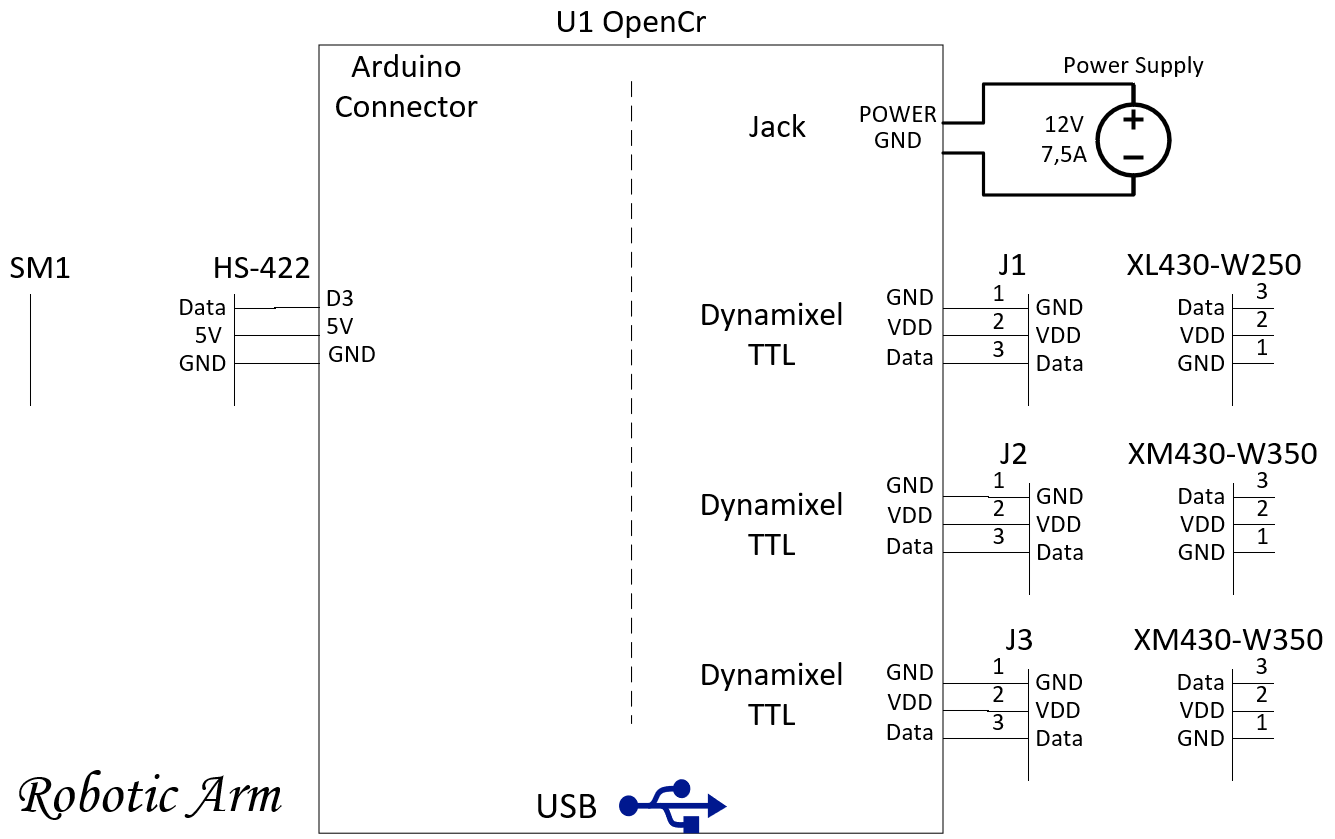
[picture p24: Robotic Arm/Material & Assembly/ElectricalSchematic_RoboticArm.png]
ElectricalSchematic - RoboticArm


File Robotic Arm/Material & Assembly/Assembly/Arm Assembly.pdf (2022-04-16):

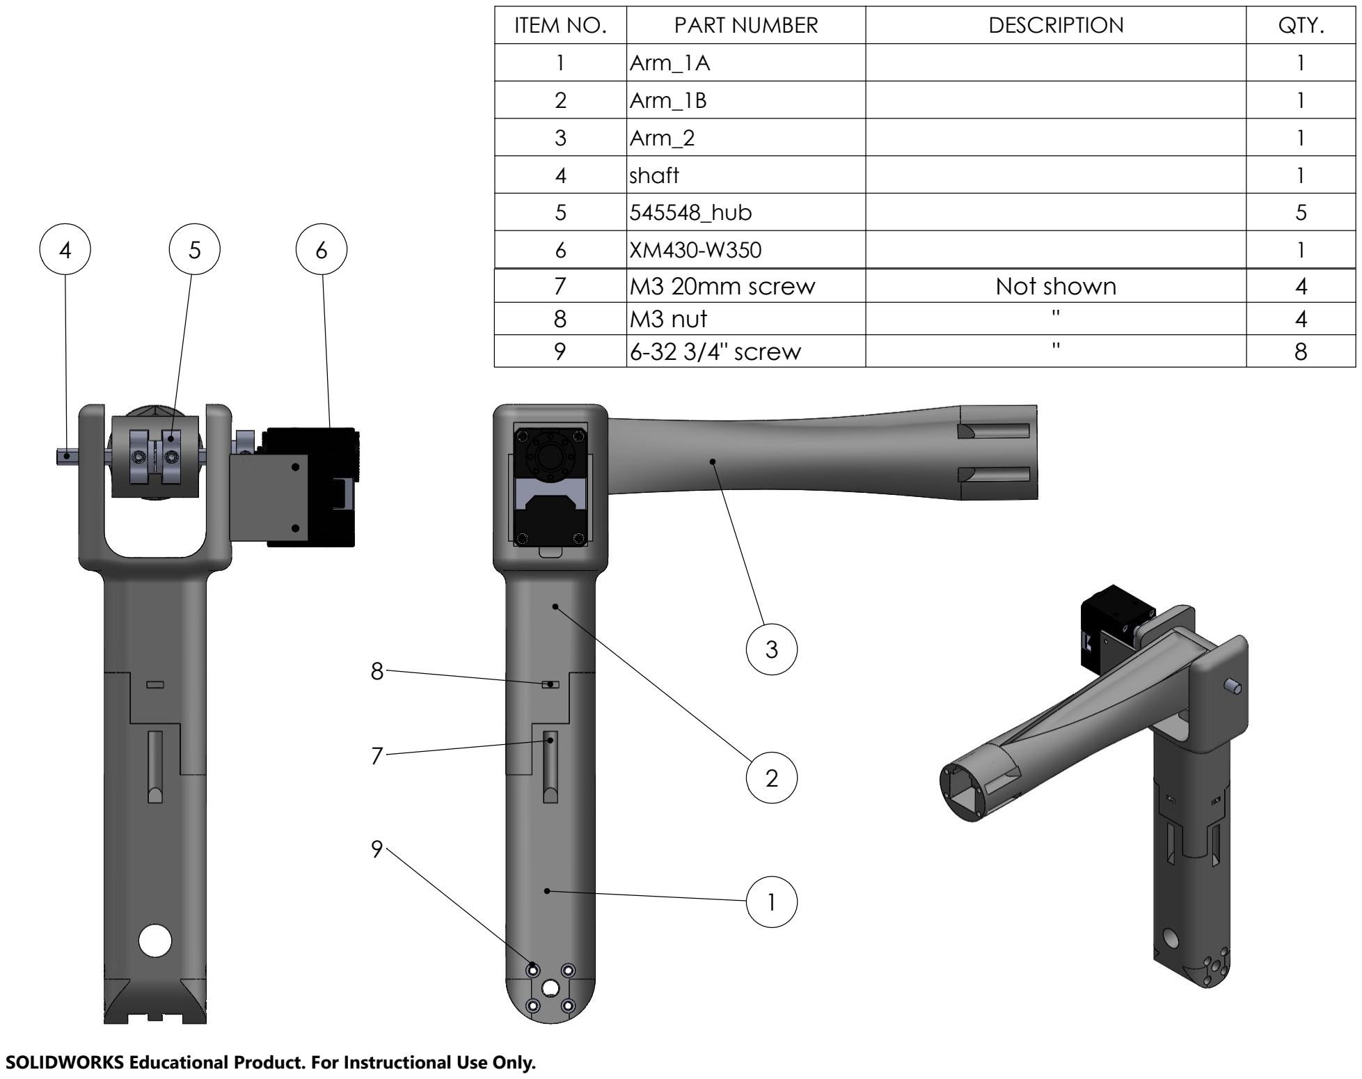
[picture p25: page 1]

ITEM NO. | PART NUMBER | DESCRIPTION | QTY.
1 | Arm_1A | | 1
2 | Arm_1B | | 1
3 | Arm_2 | | 1
4 | shaft | | 1
5 | 545548_hub | | 5
6 | XM430-W350 | | 1
7 | M3 20mm screw | Not shown | 4
8 | M3 nut | " | 4
9 | 6-32 3/4" screw | " | 8

8

7

3

2

1

9

4 | 5 | 6

SOLIDWORKS Educational Product. For Instructional Use Only.

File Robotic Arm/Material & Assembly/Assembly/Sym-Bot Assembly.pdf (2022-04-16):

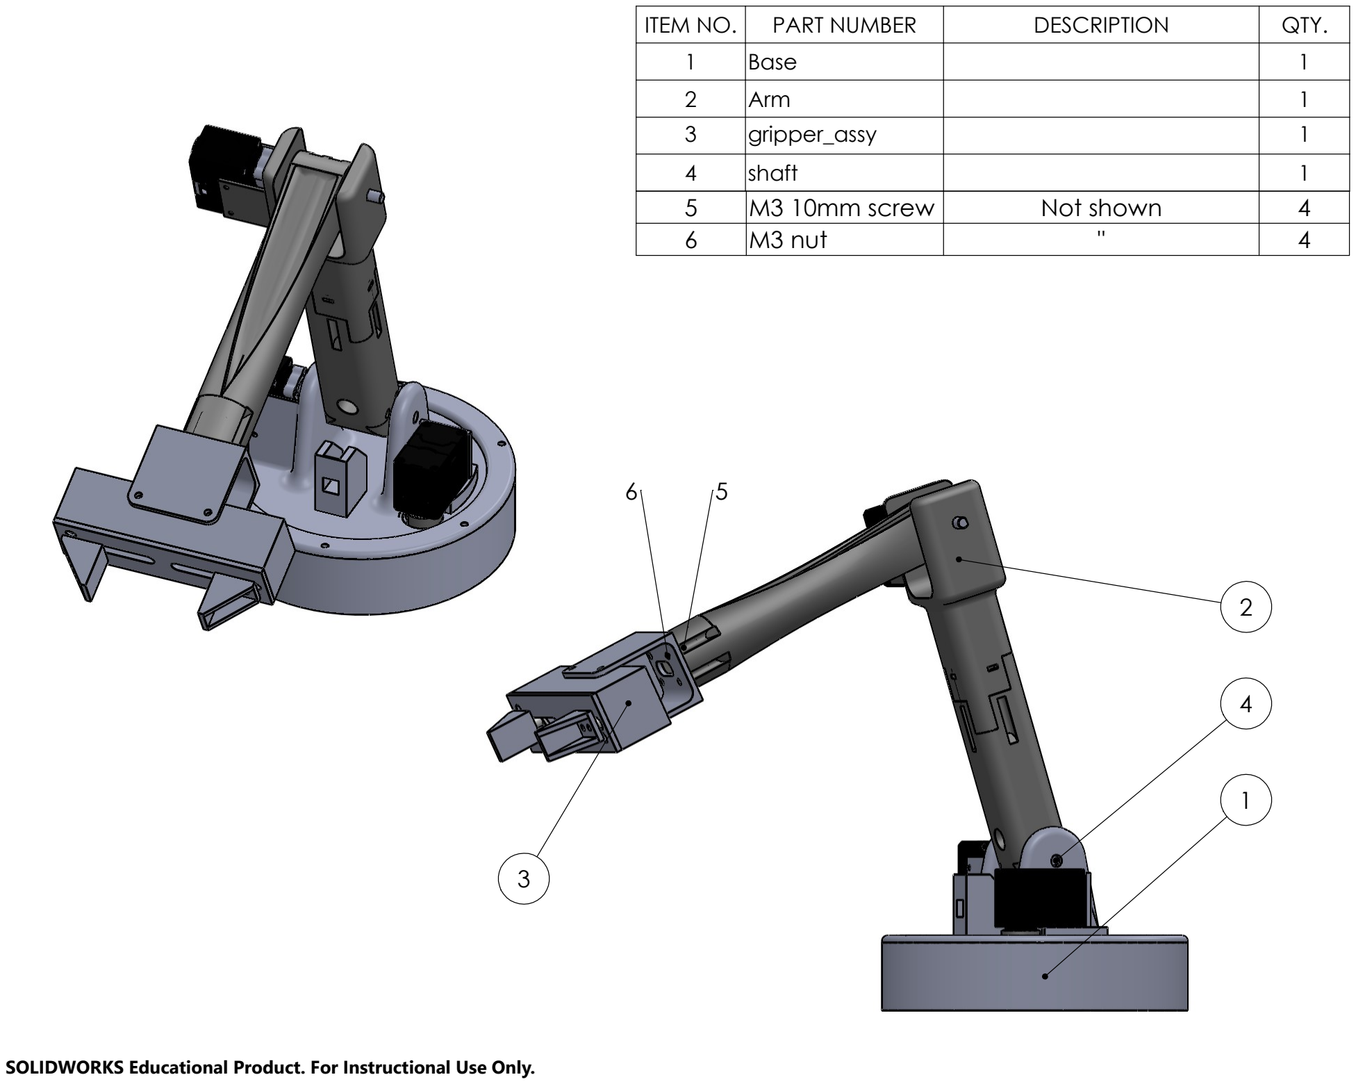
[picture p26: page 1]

1

5

4

3

2

6

ITEM NO. | PART NUMBER | DESCRIPTION | QTY.
1 | Base | | 1
2 | Arm | | 1
3 | gripper_assy | | 1
4 | shaft | | 1
5 | M3 10mm screw | Not shown | 4
6 | M3 nut | " | 4

SOLIDWORKS Educational Product. For Instructional Use Only.

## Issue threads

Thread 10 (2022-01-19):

Acquisition du matériel mécanique bras

JuThe72, 2022-01-19:

Chromlox, 2022-02-16:
Liste du matériel restant:
- Inserts (en commande)
- 6 vis pour les coupleurs de moteurs
- Petit shaft
- Deux coupleurs

Chromlox, 2022-02-17:
Matériel ajouté:
- fil groove plus court

Closed 2022-02-18.

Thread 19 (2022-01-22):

Tester les inputs du flex sensor

Chromlox, 2022-01-22:

Closed 2022-02-19.

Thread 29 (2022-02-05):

Commande des flex sensors

Chromlox, 2022-02-05:

Closed 2022-02-09.

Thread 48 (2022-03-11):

Compléter la documentation pour la partie Mécanique (Pièces et Assemblage SYM-BOT)

MicahElie, 2022-03-11:
On devrait faire un dossier spécial qui regroupe seulement ce qu'on a utilisé comme pièces 3D et l'assemblage final du bras avec notre base et préhenseur personnalisé de Sym-Bot

Closed 2022-04-17.

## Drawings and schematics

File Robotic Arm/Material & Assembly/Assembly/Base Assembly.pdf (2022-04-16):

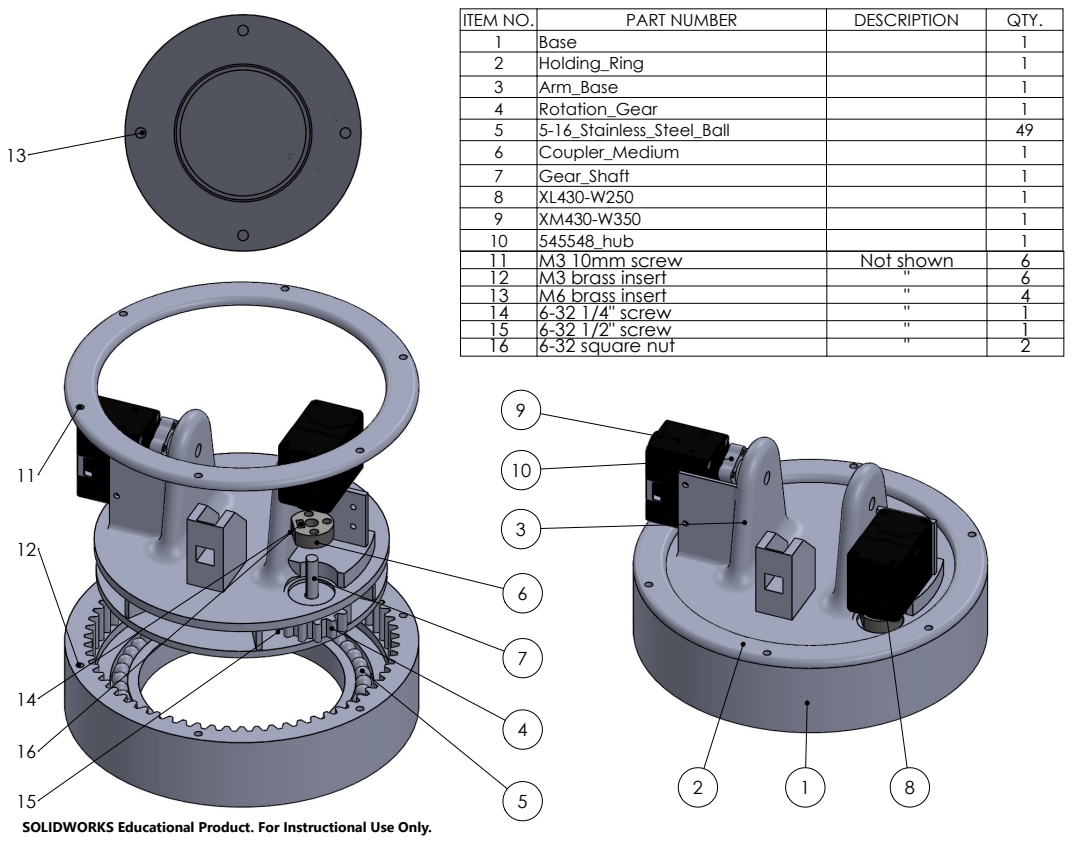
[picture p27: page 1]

ITEM NO. | PART NUMBER | DESCRIPTION | QTY.
1 | Base | | 1
2 | Holding_Ring | | 1
3 | Arm_Base | | 1
4 | Rotation_Gear | | 1
5 | 5-16_Stainless_Steel_Ball | | 49
6 | Coupler_Medium | | 1
7 | Gear_Shaft | | 1
8 | XL430-W250 | | 1
9 | XM430-W350 | | 1
10 | 545548_hub | | 1
11 | M3 10mm screw | Not shown | 6
12 | M3 brass insert | " | 6
13 | M6 brass insert | " | 4
14 | 6-32 1/4" screw | " | 1
15 | 6-32 1/2" screw | " | 1
16 | 6-32 square nut | " | 2

SOLIDWORKS Educational Product. For Instructional Use Only.

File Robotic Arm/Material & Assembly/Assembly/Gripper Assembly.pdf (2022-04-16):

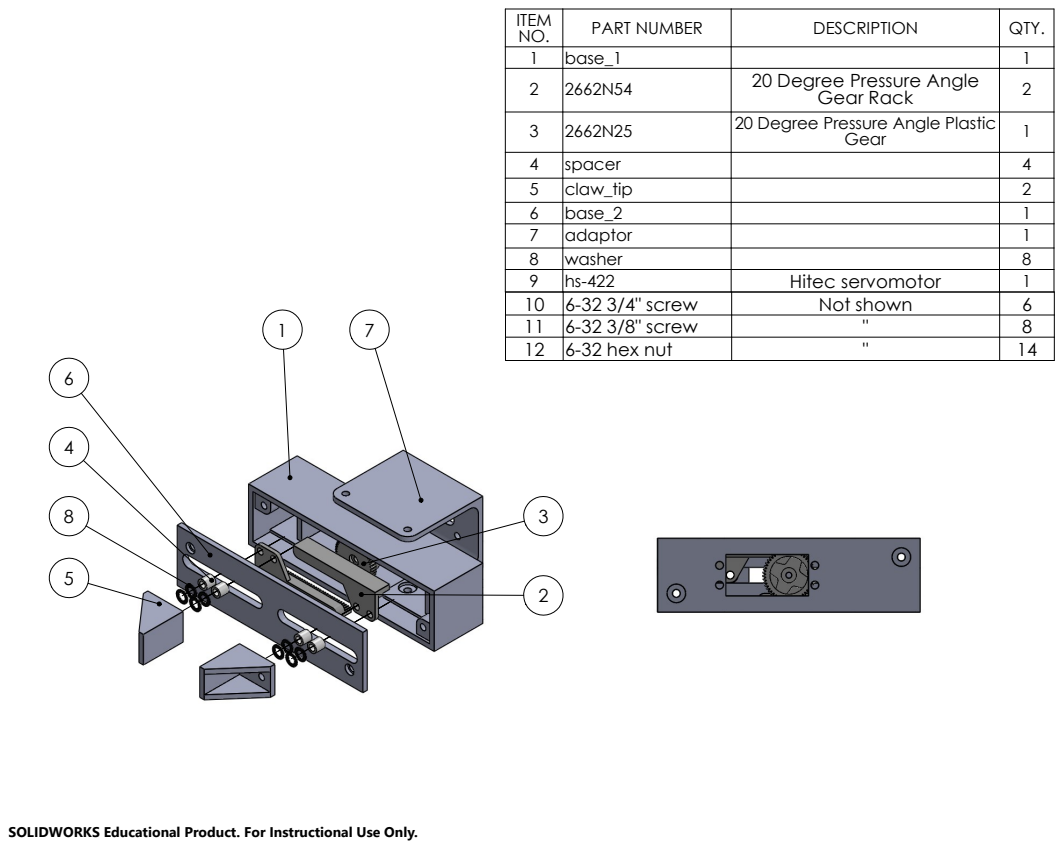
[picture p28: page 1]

ITEM NO. | PART NUMBER | DESCRIPTION | QTY.
1 | base_1 | | 1
2 | 2662N54 | 20 Degree Pressure Angle Gear Rack | 2

3 | 2662N25 | 20 Degree Pressure Angle Plastic Gear | 1

4 | spacer | | 4
5 | claw_tip | | 2
6 | base_2 | | 1
7 | adaptor | | 1
8 | washer | | 8
9 | hs-422 | Hitec servomotor | 1
10 | 6-32 3/4" screw | Not shown | 6
11 | 6-32 3/8" screw | " | 8
12 | 6-32 hex nut | " | 14

SOLIDWORKS Educational Product. For Instructional Use Only.

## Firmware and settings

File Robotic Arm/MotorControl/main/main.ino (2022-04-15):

/**
 *  Implement all the motor control part on OpenCr Board
 *    and communication management over Serial/Json
 * 
 *  Autors  : Handling-GRO, 65th promotion students, UdeS Genie de Robotique
 *  Date    : 2021-04-16
 * 
 *  Modification
 *    Initialise all the motors in setup
 *    Motor's Inheritance (Servomotor & Dynamixel)
 *    Use only CMD : GO_TO_JOINT_INDEX, GO_TO_HOME_INDEX & GO_TO_JOG
 *  Autors  : Sym-Bot, 66th promotion students, UdeS Genie de Robotique
 *  Date    : 2021-04-14
 * 
 */

// ============================================================================
// ================================= INCLUDE ==================================
// ============================================================================
#include <Arduino.h>

#include "MessageIO.h"
#include "SerialComm.h"

#include "DynamixMotor.h"
#include "ServoMotor.h"

// ============================================================================
// =============================== DEFINE/CONST ===============================
// ============================================================================
#define DEBUG 0                           // 0: Disable | 1 : Enable debug code
                                          // Comment to disable print
#define DEBUG_MSG(msg)                    // Serial.print(msg)
#define DEBUG_MSG_LN(msg)                 // Serial.println(msg)

#define BAUD              57600           // Serial's Baud

#define NbrMotorDynamixel 3
#define NbrMotorServo     1
const uint8_t NBR_MOTOR   = NbrMotorDynamixel + NbrMotorServo;

// ============================================================================
// ================================ ENUM/STRUCT ===============================
// ============================================================================
// Command index received from PI
enum CMD
{
  // ACTION IN [21, 29]
  GO_TO_JOINT_INDEX                =  1,       // USED BY SYM-BOT PROJECT
  GO_TO_HOME_INDEX                =  2,       // USED BY SYM-BOT PROJECT
  GO_TO_JOG_INDEX                 =  3,       // USED BY SYM-BOT PROJECT
  ACTION_OPEN_GRIPPER             =  5,
  ACTION_CLOSE_GRIPPER            =  6,
  ACTION_POSITION_GRIPPER         =  7,
  // SET VALUE IN [01, 09]
  SET_ZERO_POSITION_INDEX         = 11,
  SET_HOME_POSITION_INDEX         = 12,
  SET_MAX_POSITION_INDEX          = 13,
  // RETURN VALUE IN [11, 19]
  RETURN_ZERO_POSITION_INDEX      = 21,
  RETURN_HOME_POSITION_INDEX      = 22,
  RETURN_MAX_POSITION_INDEX       = 23,
  RETURN_ACTUAL_POSITION_INDEX    = 27
};

// ============================================================================
// ============================= VARIABLE GLOBALE =============================
// ============================================================================
MessageIO IO;
SerialComm SC(&Serial);
Motor *motors[NBR_MOTOR];

// ============================================================================
// ============================ DECLARED FUCNTION =============================
// ============================================================================
void init_dynamix();
void init_servo();

// ============================================================================
// =============================== SETUP/LOOP =================================
// ============================================================================
void setup() {
  // Initialise Serial Comm
  Serial.begin(BAUD);
  IO.addDevice(&SC);

  delay(10);

  // Initialise all motors and goto home each
  init_dynamix();
  init_servo();
}

void loop() {
  // MESSAGE HANDLING BLOCK, COMMUNICATION
  ControlMessage* msg = IO.readMessage(0);

  if (msg == nullptr) {
    // THIS CODE FOR TROUBLESHOOTING
    #if DEBUG == 1
      auto responce = ControlMessage(-1);
      IO.sendMessage(0,responce);
    #endif
  }
  else {
    // PAYLOAD MANAGEMENT FOR EACH ENGINE
    for (size_t i = 0; i < NBR_MOTOR; ++i) {
      // CODE FOR THE DIFFERENT OPERATIONS TO BE CARRIED OUT BY THE ENGINES
      switch (msg->getType()) {
        // VALUE THAT DOESN'T MATCH ANY OF THE CASE
        default:
          break;
        // CODE TO ACTION' MOTOR
        case GO_TO_JOINT_INDEX:
          motors[i]->go_to_degrees(msg->getPayload()[i]);
          break;
        case GO_TO_HOME_INDEX:
          motors[i]->go_to_home();
          break;
        case GO_TO_JOG_INDEX:
          if (msg->getPayload()[i] == 1)
            motors[i]->go_forward();
          else if (msg->getPayload()[i] == -1)
            motors[i]->go_backward();
          else { 
            // The arm doesn't move
          }
          break;
        case ACTION_OPEN_GRIPPER:
          if (i >= NbrMotorDynamixel)
            motors[i]->go_backward();
          break;
        case ACTION_CLOSE_GRIPPER:
          if (i >= NbrMotorDynamixel)
            motors[i]->go_forward();
          break;
        case ACTION_POSITION_GRIPPER:
          if (i >= NbrMotorDynamixel)
            motors[i]->go_to_degrees(msg->getPayload()[i]);
          break;
        
        //CODE TO SET INFORMATION
        case SET_ZERO_POSITION_INDEX:
          motors[i]->set_zero(msg->getPayload()[i]);
          break;
        case SET_HOME_POSITION_INDEX:
          motors[i]->set_home(msg->getPayload()[i]);
          break;
        case SET_MAX_POSITION_INDEX:
          motors[i]->set_max_limit(msg->getPayload()[i]);
          break;

        //CODE TO RETURN INFORMATION
        case RETURN_ZERO_POSITION_INDEX:
          msg->getPayload()[i] = (motors[i]->get_zero());
          break;
        case RETURN_HOME_POSITION_INDEX:
          msg->getPayload()[i] = motors[i]->get_home();
          break;
        case RETURN_MAX_POSITION_INDEX:
          msg->getPayload()[i] = motors[i]->get_max_limit();
          break;
        case RETURN_ACTUAL_POSITION_INDEX:
          msg->getPayload()[i] = (motors[i])->get_position();
          break;
      }
    }
    
    if(msg->getType() > 20) {
        ControlMessage response(msg->getType(), msg->getPayLoadSize(), msg->getPayload());
        IO.sendMessage(0, response);
    }

    // RELEASE msg FROM THE HEAP
    delete msg;
  }

  // delay(5);
}

// ============================================================================
// ============================ IMPLEMENT FUCNTION ============================
// ============================================================================
/* Function initialise the dynamixel motors and goto home */
void init_dynamix() {
  const uint8_t  IDs[]        = {    1,     2,     3};
  const uint16_t ZEROs[]      = {   10,  1360,  1136};
  const uint16_t HOMEs[]      = { 2047,  1920,  2160};
  const uint16_t MAXs[]       = { 4090,  2384,  3184};
  const uint16_t VELOCITYs[]  = {  128,    32,    32};
  const bool REVERSEs[]       = {false, false,  true};

  // INITIALIZE DYNAMIXEL MOTORS
  for (size_t m = 0; m < NbrMotorDynamixel; ++m) {
    if (motors[m] == nullptr) {
      motors[m] = new DynamixMotor(IDs[m], ZEROs[m], HOMEs[m], MAXs[m], VELOCITYs[m], REVERSEs[m]);
      DEBUG_MSG_LN("SET DYNAMIXEL");
    }
  }

  // GOTO HOME
  for (size_t m = 0; m < NbrMotorDynamixel; ++m) {
    motors[m]->go_to_home();

    DEBUG_MSG("Homing  ");
    DEBUG_MSG_LN(m);
  }
}

/* Function initialise the servo motors and goto home */
void init_servo() {
  const uint8_t IDs[]         = {3};

  // INITIALIZE SERVO MOTORS
  for (size_t m = NbrMotorDynamixel; m < NBR_MOTOR; ++m) {
    if (motors[m] == nullptr) {
      motors[m] = new ServoMotor(IDs[m-NbrMotorDynamixel]);
      DEBUG_MSG_LN("SET SERVO");
    }
  }

  // GOTO HOME
  for (size_t m = NbrMotorDynamixel; m < NBR_MOTOR; ++m) {
    motors[m]->go_to_home();

    DEBUG_MSG("Homing ");
    DEBUG_MSG_LN(m);
  }
}

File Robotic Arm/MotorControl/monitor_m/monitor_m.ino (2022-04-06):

/*******************************************************************************
* Copyright 2016 ROBOTIS CO., LTD.
*
* Licensed under the Apache License, Version 2.0 (the "License");
* you may not use this file except in compliance with the License.
* You may obtain a copy of the License at
*
*     http://www.apache.org/licenses/LICENSE-2.0
*
* Unless required by applicable law or agreed to in writing, software
* distributed under the License is distributed on an "AS IS" BASIS,
* WITHOUT WARRANTIES OR CONDITIONS OF ANY KIND, either express or implied.
* See the License for the specific language governing permissions and
* limitations under the License.
*******************************************************************************/

/* Authors: Taehun Lim (Darby) 
 * Modify
 */

#include <DynamixelWorkbench.h>

#if defined(__OPENCM904__)
  #define DEVICE_NAME "3" //Dynamixel on Serial3(USART3)  <-OpenCM 485EXP
#elif defined(__OPENCR__)
  #define DEVICE_NAME ""
#endif   

#define SERIAL_BAUD      57600
const String DXL_BAUD = "57600";

#define STRING_BUF_NUM 64
String cmd[STRING_BUF_NUM];
uint8_t len = 0;

DynamixelWorkbench dxl_wb;
uint8_t get_id[16];
uint8_t scan_cnt = 0;
uint8_t ping_cnt = 0;

bool isAvailableID(uint8_t id);
uint8_t split(String data, char separator, String* temp);
void printInst();

void setup() 
{
    Serial.begin(SERIAL_BAUD);
    while(!Serial); // Open a Serial Monitor  

    printInst();
}

void loop() 
{
  const char *log = NULL;
  bool cmdSucceedec = false;

  if (Serial.available())
  {
      String read_string = Serial.readStringUntil('\n');
      Serial.println("[CMD] : " + String(read_string));

      read_string.trim();

      len = split(read_string, ' ', cmd);

      if (cmd[0] == "help")
      {
        printInst();
      }
      else if (cmd[0] == "begin")
      {
        if (cmd[1] == '\0')
          cmd[1] = DXL_BAUD;

        uint32_t baud = cmd[1].toInt();
        cmdSucceedec = dxl_wb.init(DEVICE_NAME, baud);
        if (cmdSucceedec == false)
        {
          Serial.println(log);
          Serial.println("Failed to init");
        }
        else
        {
          Serial.print("Succeed to init : ");
          Serial.println(baud);  
        }
      }
      else if (cmd[0] == "end")
      {        
        return;
      }
      else if (cmd[0] == "scan")
      { 
          if (cmd[1] == '\0')
              cmd[1] = String("253");

          uint8_t range = cmd[1].toInt();
          cmdSucceedec = dxl_wb.scan(get_id, &scan_cnt, range);
          if (cmdSucceedec == false)
          {
              Serial.println(log);
              Serial.println("Failed to scan");
          }
          else
          {
              Serial.print("Find ");
              Serial.print(scan_cnt);
              Serial.println(" Dynamixels");

              for (int cnt = 0; cnt < scan_cnt; cnt++)
              {
                  Serial.print("id : ");
                  Serial.print(get_id[cnt]);
                  Serial.print(" model name : ");
                  Serial.println(dxl_wb.getModelName(get_id[cnt]));
              }
          }  
      }
      else if (cmd[0] == "ping")
      {
          if (cmd[1] == '\0')
            cmd[1] = String("1");

          uint8_t id       = cmd[1].toInt();
          // get_id[ping_cnt] = cmd[1].toInt();
          uint16_t model_number = 0;

          cmdSucceedec = dxl_wb.ping(id, &model_number, &log);
          // cmdSucceedec = dxl_wb.ping(get_id[ping_cnt], &model_number, &log);
          if (cmdSucceedec == false)
          {
              Serial.println(log);
              Serial.println("Failed to ping");
          }
          else
          {
              // ping_cnt++;

              Serial.println("Succeed to ping");
              Serial.print("id : ");
              Serial.print(id);
              // Serial.print(get_id[ping_cnt]);
              Serial.print(" model_number : ");
              Serial.println(model_number);
          }
      }
      else if (cmd[0] == "position")
      {
          int32_t data     = 0;

          if(cmd[1] != '\0')
          {
              uint8_t id = cmd[1].toInt();
              if(isAvailableID(cmd[1].toInt()))
              {
                  cmdSucceedec = dxl_wb.itemRead(id, "Present_Position", &data, &log);
                  if (cmdSucceedec == false)
                  {
                      Serial.println(log);
                      Serial.println("Failed to read");
                      return;
                  }
                  else
                  {
                      Serial.println(log);
                      Serial.print("read position : ");
                      Serial.println(data);
                  }
              }
          }
          else
          {
              for (size_t dxl_cnt = 0; dxl_cnt < (scan_cnt + ping_cnt); ++dxl_cnt)
              {
                  Serial.println("============ Present Position ============");
                  cmdSucceedec = dxl_wb.itemRead(get_id[dxl_cnt], "Present_Position", &data, &log);
                  if (cmdSucceedec == false)
                  {
                      Serial.print("Failed to read : ");
                      Serial.println(log);
                      return;
                  }
                  else
                  {
                      Serial.print(get_id[dxl_cnt]);
                      Serial.print(" : ");
                      Serial.println(data);
                  }
                  delay(10);
              }
          }
      }
      else if (isAvailableID(cmd[1].toInt()))
      {
          if (cmd[0] == "control_table")
          {
              uint8_t id = cmd[1].toInt();

              const ControlItem *control_item =  dxl_wb.getControlTable(id);
              uint8_t the_number_of_control_item = dxl_wb.getTheNumberOfControlItem(id);

              uint16_t last_register_addr = control_item[the_number_of_control_item-1].address;
              uint16_t last_register_addr_length = control_item[the_number_of_control_item-1].data_length;

              uint32_t getAllRegisteredData[last_register_addr+last_register_addr_length];

              if (control_item != NULL)
              {
                  cmdSucceedec = dxl_wb.readRegister(id, (uint16_t)0, last_register_addr+last_register_addr_length, getAllRegisteredData, &log);
                  if (cmdSucceedec == false)
                  {
                    Serial.println(log);
                    return;
                  }
                  else
                  {
                      for (int index = 0; index < the_number_of_control_item; index++)
                      {
                          uint32_t data = 0;
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

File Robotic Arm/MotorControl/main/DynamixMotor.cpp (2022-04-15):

#include "DynamixMotor.h"

DynamixelWorkbench dxl_wb;  // create DynamixelWorkbench object to control dynamixelS

/**
 * This function initialises a DynamixMotor object
 * 
 * @param id contains the ID of dynamixel motor
 * @param zero the position of motor corresponding to its zero (STEP)
 * @param home the position of motor corresponding to home (STEP)
 * @param max_limmit the position of motor corresponding to its max value (STEP)
 * @param speed the speed of motor corresponding to its velocity
 * @param reverse indicates if motor has to turn the other side
*/
DynamixMotor::DynamixMotor(uint8_t id, uint16_t zero, uint16_t home, uint16_t max_limit, uint16_t speed, bool reverse) {
    this->id = id;

    this->zero      = zero;
    this->home      = home;
    this->max_limit = max_limit;
    this->velocity  = speed;
    this->step      = speed >> 2;
    this->reversed  = reverse;

    cmdSucceeded = dxl_wb.init(DEVICE_NAME, baud);
    cmdSucceeded = dxl_wb.ping((int8_t)id, &model_number, &log);

    if (reverse)
        cmdSucceeded = dxl_wb.setReverseDirection(id, &log);
    else
        cmdSucceeded = dxl_wb.setNormalDirection(id, &log);

    cmdSucceeded = dxl_wb.jointMode(id, this->velocity, 0, &log);    
    cmdSucceeded = dxl_wb.ledOn((uint8_t)id, &log);

    /* Unit	0.229 [rev/min]	Sets velocity of the Profile
       * Unit	1 [msec]	Sets the time span for the Profile
       * Range	0 ~ 32767	‘0’ represents an infinite velocit */
    cmdSucceeded = dxl_wb.itemWrite(id, "Profile_Velocity", this->velocity, &log);
    /* Unit	214.577 [rev/min2]	Sets acceleration of the Profile
       * Unit	1 [msec]	Sets accelerating time of the Profile
       * Range	0 ~ 32767	‘0’ represents an infinite acceleration */
    cmdSucceeded = dxl_wb.itemWrite(id, "Profile_Acceleration", this->accelaration, &log);

    // TO ADD FOR MORE SECURITY
    // cmdSucceeded = dxl_wb.itemWrite(id, "Max_Position_Limit", max_limit, &log);
    // cmdSucceeded = dxl_wb.itemWrite(id, "Min_Position_Limit", zero, &log);
}

void DynamixMotor::go_to(int16_t pos) {
    if (pos < zero)
        pos = zero;
    if (pos > max_limit)
        pos = max_limit;
    position = pos;
    dxl_wb.goalPosition(id, (int32_t)pos, &log);
};

// CONVERT STEP TO DEGREES := 4096 STEP / 360 DEGREES = 11,3778 STEP BY DEGREES
void DynamixMotor::go_to_degrees(int16_t pos) { this->go_to((pos * 11.3778) + zero); }
void DynamixMotor::go_to_home() { this->go_to(home); }

void DynamixMotor::go_forward() {
    int32_t pos = position;
    // int32_t pos = get_position();        // DON'T WORK WITH GRIPPER
    pos -= step;
    go_to(pos);
};

void DynamixMotor::go_backward() {
    int32_t pos = position;
    // int32_t pos = get_position();        // DON'T WORK WITH GRIPPER
    pos += step;
    go_to(pos);
}

int16_t DynamixMotor::get_position() {
    int32_t data = 0;
    cmdSucceeded = dxl_wb.itemRead(id, "Present_Position", &data, &log);
    return data;
}

// DONT USE IN SYM-BOT PROJECT
int16_t DynamixMotor::get_home_offset() {
    int32_t data = 0;
    cmdSucceeded = dxl_wb.itemRead(id, "Homing_Offset", &data, &log);
    return data;
}

void DynamixMotor::setHomingOffset(int16_t pos) {
    cmdSucceeded = dxl_wb.itemWrite(id, "Homing_Offset", pos, &log);
}

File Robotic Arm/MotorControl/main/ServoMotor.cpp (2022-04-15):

#include "ServoMotor.h"

/**
 * This function initialises a ServoMotor object
 * 
 * @param pin // attaches the servo on this pin to the servo object
 * @param home the position of motor corresponding to home (DEGREES)
*/
ServoMotor::ServoMotor(uint8_t pin, uint16_t home) {
    this->pin = pin;
    this->home = home;
    servo.attach(pin);
    #if DEBUG == 1
        if (servo.attached())
            Serial.print("Ready motor : ");
        else
            Serial.print("Not ready motor : ");
        Serial.println(pin);
    #endif
};

// servo.write(angle), angle: the value to write to the servo, from 0 to 180
void ServoMotor::go_to(int16_t pos) { servo.write(pos); };
void ServoMotor::go_to_degrees(int16_t pos) { this->go_to(pos); }
void ServoMotor::go_to_home() { this->go_to(this->home); }
void ServoMotor::go_forward() { this->go_to(30); };
void ServoMotor::go_backward() { this->go_to(180); }

// Return : The angle of the servo, from 0 to 180 degrees.
int16_t ServoMotor::get_position() { return servo.read(); }
// DONT USE IN SYM-BOT PROJECT
int16_t ServoMotor::get_home_offset() { return 0; }
void ServoMotor::setHomingOffset(int16_t pos) { ; }

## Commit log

2022-01-18 Adding - Handling-GRO files
    Here we add code from another projet, Handling-GRO. This will be the foundation for the rest of the project
    [1XTendeurPART1.STL, 1XTendeur_PART2.STL, 1X_Base_Controler.STL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]
2022-01-27 Add- Base
    CAD pour la nouvelle base
    [Assemblage1.SLDASM, Cercle_maintient.SLDPRT, M2-16mm_91292A002_TYPE 18-8 SS SOCKET HEAD CAP SCREW.SLDPRT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]
2022-01-29 Base V2 (Conception de la base du bras)
    [Bille.SLDPRT, Cercle_maintient_V2.SLDPRT, Plateau_bas_V2.SLDPRT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]
2022-02-02 Finalisation de la base ( Closes #16 )
    Modélisation terminée, il manque l'impression de quelques pièces.
    [Base_bras_V2.STL, Cercle_maintient_V2.STL, Plateau_bas_V2.SLDPRT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]
2022-02-14 Ajustement de la conception ( #4 )
    [Assemblage1.SLDASM, Roue_controle.SLDPRT, Roue_controle_V2.STL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]
2022-02-14 Lecture de fichiers CSV ( #32 )
    [VArm1_bolt_V2.STL]
2022-02-16 ControlJointSimpliee( #34)
    Controle en joint sans passer par Qt
2022-02-21 Controle Joint ( #34 )
    Controle en joint des moteur directement avec les fonction de dynamyxel ; création de test simplifier pour la présentation
    [Coupler_1.SLDPRT, shaft_22mm.SLDPRT]
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2022-02-22 Code pour la démo de la livraison 1
2022-02-26 -Setup pour Flex sur Arduino Nano avec PlatformIO
    [main.cpp]
2022-03-16 Ménage et classes ( #56 )
    Nettoyage des fonction inutilisé et ajout des classe Motor et Servomotor
2022-03-16 Update README.md
    Ajout des liens pour les équipements
2022-03-16 Ménage Doc ( #45 )
    [1XTendeurPART1.STL, 1XTendeur_PART2.STL, 1X_Base_Controler.STL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]
2022-03-17 -Adding ESP32 Bluetooth Serial Communication of Sensors #36
    On peut maintenant print les données des capteurs du gant par Bluetooth!
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2022-03-23 Gripper ( #42 )
    [base_1.SLDPRT, base_1.STL, base_2.SLDPRT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]
2022-03-23 Repair sync git
    all was broken
    [BluetoothComm.py, ControlMessage.py, main.ino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]
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2022-03-27 test de jogMode fonctionnel
    Manque test pour répétition de commande
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2022-03-28 -Structure de l'envoi des données BT terminée
    -Ajout d'un indicateur LED pour la position de la main
    -Nettoyage de commentaires inutiles dans fonction IMU
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2022-03-29 Entrainement de l'AI part 1 ( #60 )
    Quelques éléments sont manquants, mais les fonctions de bases permettant l'enregistrement des positions ont été complétées (mais non-testées)
2022-03-29 Gripper V2
    Mise à jour des CADs du préhenseur
    [base_2.SLDPRT, claw_rack.SLDPRT, claw_rack_V2.STL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]
2022-03-30 AI Mode ( #60 )
    Bug correction,
    [BluetoothComm.py, main.py, test_translate.py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]
2022-03-30 Test + Déverminage du code de collection
    Ça fonctionne.
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2022-03-31 -Ajout des fonctions bouton pour le mode #65
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2022-04-02 - Ajout d'une structure Hand qui regroupe toutes les données des capteurs
    - Ajout d'un protocole de vérification d'erreurs avec DEL
2022-04-03 - Ajout de la DEL qui indique le mode
    - Remplacement de ';' par '|' pour la séparation de comm
2022-04-03 -Modification du split du message ';' -> '|'
    Je voulais que ça ait l'air d'un tableau...
2022-04-03 -Réorganisation des dossiers
    [1XTendeurPART1.STL, 1XTendeur_PART2.STL, 1X_Base_Controler.STL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]
2022-04-03 -fixes README principal et ajout de liens
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2022-04-06 #50
    Déplacement des dossier de l'interface dans Application pour faciliter la communication
2022-04-06 AI save_example (Semi-bloquant)
    Fonctionne presque; Pas une solution idéale, mais devrait suffire pour l'entraînement de l'AI
2022-04-08 Ajust function type go_to and ajust velocity
    Éviter le débordement d'une valeur négative
    Ajout d'un paramètre de vitesse dans le constructeur et diminution de l'accélération
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2022-04-08 Update interface.py
    Updated Change_mode(args) function so that it would not only change which button is in mint, but also which set of coordinates is shown. Also changed the grid value of all J1/J2/J3 objects so that th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
2022-04-09 Moving Joint functions
    Must add comm or motor functions to this. As well as motor names...
2022-04-09 Dossiers Update et ajout d'espaces dans les noms
    Material & Assembly -> Robotic Arm
    [1XTendeurPART1.STL, 1XTendeur_PART2.STL, 1X_Base_Controler.STL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]
2022-04-09 Fix Robotic Arm and Glove UI links
2022-04-09 Train Mode OK?
    Devrait être en mesure d'entrainer l'AI. J'en ai aussi profiter pour faire un peu de menage dans la sélection du mode (translate)
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2022-04-10 Completed jog functions
    Still not 100% sure if I used the right motor ids, if someone could double-check, that would be great.
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2022-04-12 Juste quelques changements pour mes vues du rapport
    [Cercle_maintient_V2.SLDPRT, Coupler_1.SLDPRT, Plateau_bas_V2.SLDPRT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]
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2022-04-12 Ajustement coupleur
    [coupler_joint_V2.SLDPRT, coupler_joint_V3.STL]
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2022-04-15 Release Update - Robotic Arm Code
    Ajout de commentaire au niveau du main et des fichiers moteurs
    Activer le revoir d'information via la communication Serial
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2022-04-15 Update README - GloveUI
    Ajout d'une description pour la section « Alternative »
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2022-04-15 +Note about IMU usage in the project
    and others fixes
    [main.cpp]
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2022-04-16 Assembly Cleanup (Part 1)
    [40x40x10 DC Fan.SLDPRT, 5-16_Stainless_Steel_Ball.SLDPRT, 535198.SLDPRT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]
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2022-04-16 Assembly Cleanup (Part 2)
    [1XTendeurPART1.STL, 1XTendeur_PART2.STL, 1X_Base_Controler.STL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]
2022-04-16 Assembly Cleanup (Part 3)
    [Arm.SLDASM, Arm.SLDDRW, Arm_Base.SLDPRT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]
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

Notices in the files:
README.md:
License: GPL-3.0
